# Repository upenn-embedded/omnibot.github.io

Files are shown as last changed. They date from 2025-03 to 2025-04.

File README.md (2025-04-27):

<div id="slideshow" style="width:100%; max-width:700px; margin: auto; position: relative; height: 450px;">
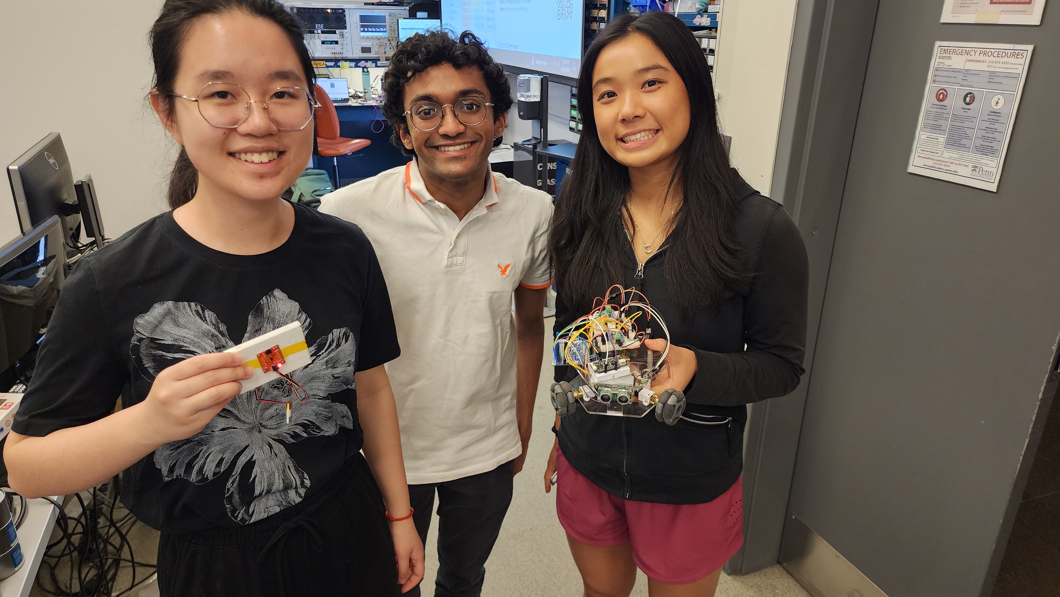
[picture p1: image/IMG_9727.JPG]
  
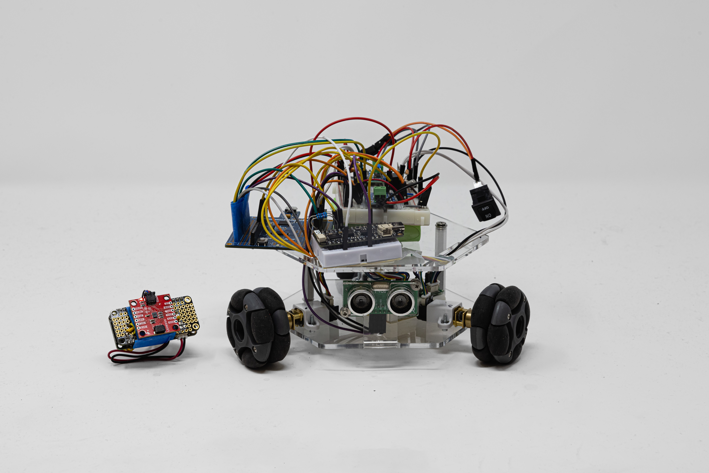
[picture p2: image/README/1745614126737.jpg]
  
  
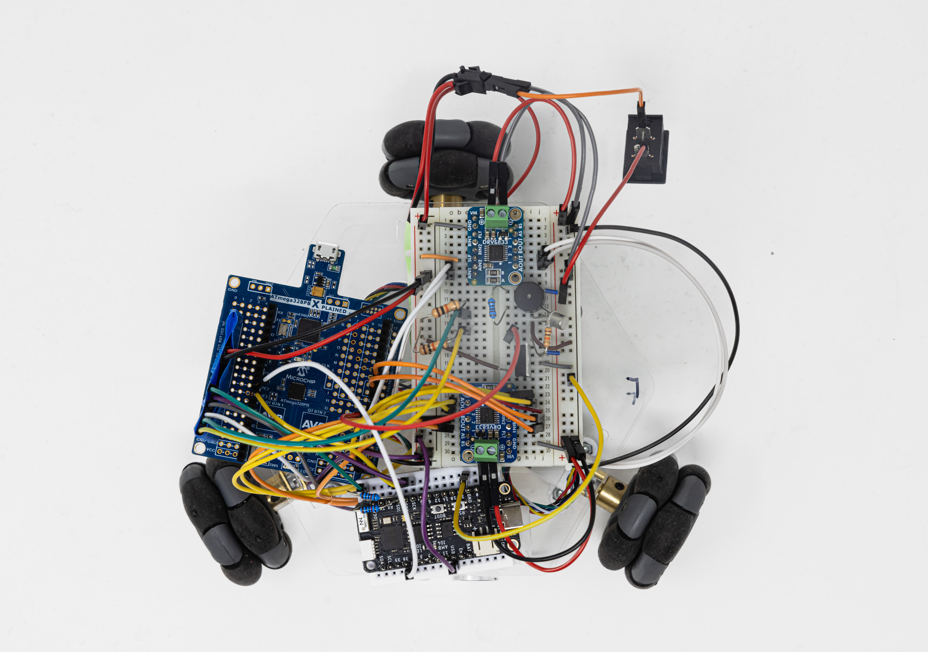
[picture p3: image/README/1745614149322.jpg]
  
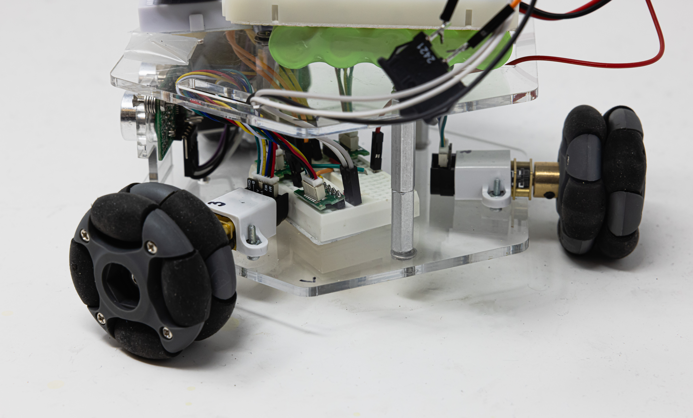
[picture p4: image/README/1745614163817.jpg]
  
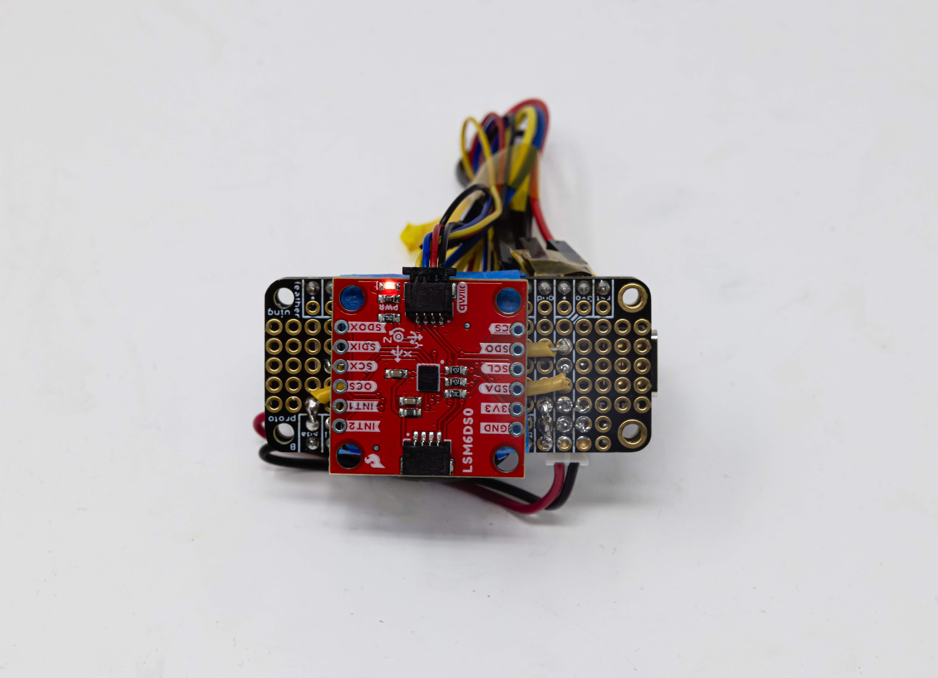
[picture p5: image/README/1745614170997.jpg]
  
  
</div>

<script>
let slides = document.querySelectorAll('#slideshow img');
let current = 0;
setInterval(() => {
  slides[current].style.opacity = 0;
  current = (current + 1) % slides.length;
  slides[current].style.opacity = 1;
}, 3000); // changes every 3 seconds
</script>

<br><br><br>

# final-project-OmniBot
    * Team Number: Team 9
    * Team Name: Oranges
    * Team Members: Izzy, Helena, and Vidhu
    * GitHub Repository URL: [https://github.com/upenn-embedded/final-project-s25-oranges](https://github.com/upenn-embedded/final-project-s25-oranges)
    * GitHub Pages Website URL: [https://upenn-embedded.github.io/omnibot.github.io/](https://upenn-embedded.github.io/omnibot.github.io/)

## Final Project Proposal

### 1. Abstract

Our final project is a gesture controlled omnidirectional robot designed to enable users to control a mobile robot’s movement using intuitive hand gestures. The robot will use omni wheels for enhanced maneuverability, allowing for movement in multiple directions (forward, backward, lateral, and diagonal) without the need for steering or reorientation. This is unlike traditional wheels, which require turning to change direction. Additionally, the OmniBot will include a collision detection system using an ultrasonic sensor that triggers a buzzer when obstacles are detected.

### 2. Motivation

Controlling robots using traditional joysticks or remotes can often be challenging and unintuitive, especially for new users. To address this, our project introduces a gesture-based control system that simplifies robot navigation while enhancing flexibility and precision through the use of omni wheels. The robot has the ability to move smoothly in multiple directions, including lateral and diagonal motion. Additionally, the inclusion of a collision detection system enhances the project's safety features by enabling the robot to identify and respond to nearby obstacles. These features make the project particularly valuable in practical applications like exploration and assistive robots for hazardous. The combination of intuitive gesture control and omni wheel movement offers a unique blend of precision, responsiveness, and user-friendly control.

### 3. System Block Diagram

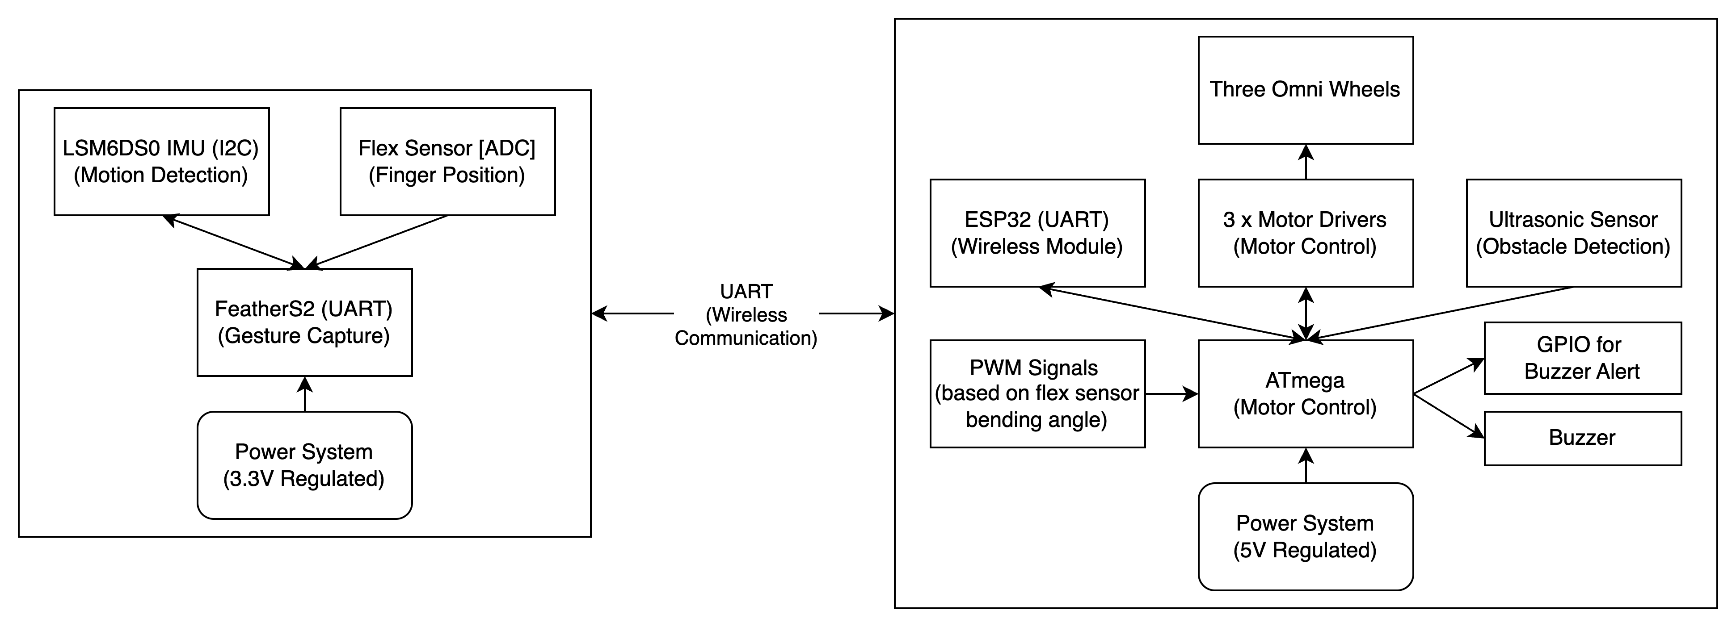
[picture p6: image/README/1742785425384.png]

Our system consists of two primary subsystems: the **Gesture Capture System** and the **Motor Control System** for the OmniBot. They utilize various communication protocols including I2C, ADC, UART, PWM, and GPIO. Additionally, regulated power supplies are integrated into both subsystems to deliver stable voltage levels.

The **Gesture Capture System** is centered around FeatherV2/FeatherS2, which manages both sensor inputs and wireless data transmission. It will handle gesture capture by interfacing with the LSM6DS0 IMU and Flex Sensor, while simultaneously transmitting control data to the OmniBot's ESP32 module via UART.

LSM6DS0 IMU is responsible for detecting hand motion and orientation. It uses the I2C to communicate with FeatherV2. The Flex Sensor detects the degree of bending in the user's fingers, then it generates an analog voltage that is read directly by the FeatherV2’s ADC. The ADC values are mapped to speed control commands, allowing different modes of motor speed with intuitive control. A FeatherS2 will be used to receive the data from the FeatherV2 via ESP-NOW and transmit the IMU values to the ATMega via SPI.

The **Motor Control System** is built around the ATmega328PB microcontroller, which handles motor control, obstacle detection, and alert systems. The FeatherS2 is mounted on the OmniBot and is the wireless receiver, communicating with the FeatherV2 on the wearable controller.

Motor control is achieved using two motor drivers (each driver can control 2 motors) that interface with ATMega. The motor drivers then manage the three omni wheels respectively, enabling movement in multiple directions. The ATMega generates PWM signals that control the direction of the motors and the speed is controlled through the duty cycle. The duty cycle will dynamically adjust based on the bending angle from the flex sensor and motor direction will change depending on the hand motion detected from the IMU.

The rover also features an ultrasonic sensor for obstacle detection. The sensor communicates with ATMega using GPIO pins for both the trigger and echo signals. When an obstacle is detected within a specified range, the ATMega will activate a buzzer via a dedicated GPIO output, alerting the user of the presence of an obstacle.

For the communication protocol, I2C links LSM6DS0 IMU to FeatherV2. The ADC on FeatherV2 is used to read variable voltage signals from the Flex Sensor. ESP-NOW is employed for wireless communication between the two Feather boards. ATMega generates PWM signals at different duty cycles to modulate motor speed and direction. GPIO connections are used for the ultrasonic sensor and the buzzer.

For power regulation, the Feather requires a 3.3V regulated power supply. Meanwhile, the 5V regulated power supply in the rover system delivers stable power to the ATMega328PB, motor drivers, ultrasonic sensor, and buzzer. A 6V battery is used to power our entire system. The motors we use are 6V and are able to pull as much current as needed from the battery pack. A 5V voltage regulator is used to buck down the 6V to 5V for our ATMega and peripherals. This separation of power systems ensures reliable performance, minimizes electrical noise, and protects components from voltage instability.

### 4. Design Sketches

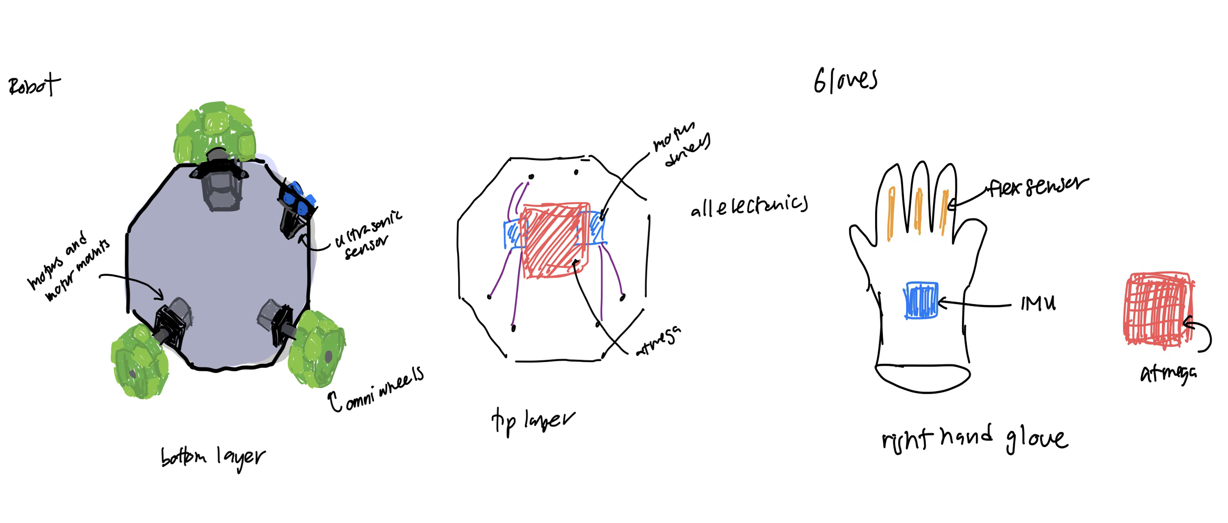
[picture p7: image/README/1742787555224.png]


For our design, the OmniBot's base uses omni wheels for enhanced motion in multiple directions. The use of an ultrasonic sensor for obstacle detection ensures improved environmental awareness. The top layer of the robot houses all essential electronics, including the ATMega board, motor drivers, and power distribution system. On the glove controller, the IMU is positioned centrally on the back of the hand to accurately detect wrist movements, and the flex sensors are embedded along the fingers to track bending angles for speed control.

### 5. Software Requirements Specification (SRS)

The software for the gesture-controlled rover robot will be able to process real-time motion and detect different gestures, wirelessly transmit commands, and be able to precisely control the rover. This can be broken down into three different subsystems:  gesture controller, rover control system, and collision detection system. The wearable gesture controller detects user gestures and transmits these movements wirelessly. The rover control system will be able to intercept these commands and control the rover's movement using predefined gesture mappings. The collision detection system monitors the rover/s surroundings and alerts the users of any obstacles. Key requirements include gesture recognition accuracy, reliable wireless communication, precise motor control, and responsive collision detection

**5.1 Definitions, Abbreviations**

*IMU (Inertial Measurement Unit):* A sensor that combines an accelerometer and a gyroscope to track orientation, acceleration, and angular velocity. In this project, it is used to detect hand gestures such as tilts and wrist rolls.

*Flex sensor:* A sensor that changes its resistance based on the amount of bending or flexing. It is used here to detect finger position and aid in gesture control.

*Feather ESP32:* The wireless communication module using ESP-NOW to transmit data between the wearable controller and the robot.

*Ultrasonic Sensor:* A distance sensor that uses sound waves to detect objects. It is used here for obstacle detection on the robot.

**5.2 Functionality**

<table>
  <thead>
    <tr>
      <th style="width:100px;">ID</th>
      <th>Description</th>
    </tr>
  </thead>
  <tbody>
    <tr>
      <td>SRS-01</td>
      <td>The IMU and flex sensors shall track predefined hand gestures (forward, backward, left, and right tilt, wrist roll, and open palm) within 200ms.</td>
    </tr>
    <tr>
      <td>SRS-02</td>
      <td>The ATmega328PB shall process the IMU data and classify gestures based off of certain threshold values correctly.</td>
    </tr>
    <tr>
      <td>SRS-03</td>
      <td>The ESP32 will transmit gesture data from the user to the robot with latency &lt; 200ms.</td>
    </tr>
    <tr>
      <td>SRS-04</td>
      <td>The robot shall have three speed modes controlled based on the angular velocity detected from wrist rolling.</td>
    </tr>
    <tr>
      <td>SRS-05</td>
      <td>The ultrasonic sensor shall detect obstacles within 5–100 cm. If an obstacle is within 20 cm, the robot will stop, ignore commands, and the LED will turn red. Once cleared, the robot resumes movement, and the LED turns green.</td>
    </tr>
    <tr>
      <td>SRS-06</td>
      <td>The entire system will run independently on the ATmega328PB without the need of an external computer.</td>
    </tr>
    <tr>
      <td>SRS-07</td>
      <td>If wireless connection is lost, the robot shall automatically stop within 500ms.</td>
    </tr>
  </tbody>
</table>

### 6. Hardware Requirements Specification (HRS)

The hardware for the gesture controller rover will allow it to move freely in many directions as well as sense the motion of the controller. Additionally, it will be able to sense obstacles ahead using an ultrasonic sensor.

**6.1 Definitions, Abbreviations**
*Feather ESP32:* Board for wireless communication

*ATMega328PB:* Main microcontroller on the rover

**6.2 Functionality**

| ID | Description |
| --- | --- |
| HRS-01 | The rover must be able to run for at least 15 minutes continuously. |
| HRS-02 | The ultrasonic sensor must be able to accurately detect obstacles within 5-100 cm. |
| HRS-03 | The motors must be able to move the rover at varying speeds. |
| HRS-04 | The rover must be able to move in perpendicular directions without needing to turn using the omni wheels. |
| HRS-05 | The flex sensor must be able to control the speed of the rover using an ADC. |
| HRS-06 | Motion of the IMU must translate into motion of the rover. |
| HRS-07 | The two ESP32 boards must be able to wirelessly communicate with each other directly. |
| HRS-08 | The ESP32 and ATMega328PB must be able to communicate using SPI. |

### 7. Bill of Materials (BOM)
This is a general list of our bill of materials. A more detailed list can be found [here](https://docs.google.com/spreadsheets/d/1VVz9bghLVpC_rwVTz9ZApd166kRQwFx1JgdSo3LERfQ/edit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). We used an ATMega329PB, Feather ESP32 V2, Feather ESP32 S2, LM6DS0 IMU, US-10 Ultrasonic sensor, 3 6V Polulu motors with motor mounts and enocder wires, 6V battyer, 2 DRV8871 motor drivers, and 3 omni wheels.

### 8. Final Demo Goals

On Demo Day, we will build an obstacle course for our rover to test in. Someone will wear the controller and manuver the rover around obstacles. Part of the test will include getting close to an obstacle and stopping before a collision. The test will conclude when the rover is successfully able to get to the end of the obstacle course.

### 9. Sprint Planning

| Milestone  | Functionality Achieved |
| --- | --- | --- |
| Sprint #1  | 1. Developed Wearable Controller Prototype using the FeatherS2.<br />2. Implemented motion sensing algorithms with the  LSM6DS0 IMU.<br />3. Integrated the Flex Sensor for ADC-based speed control.<br />4. Developed basic motor control firmware for the ATmega using PWM signals for speed and direction. | 
| Sprint #2  | 1. Established UART Communication between the two FeatherS2 boards.<br />2. Integrated gesture detection logic with motor speed control via PWM signals.<br />3. Assembled hardware components: Motor Drivers, Omni Wheels, and Power Systems.<br />4. Conducted movement tests to verify functionality. |
| MVP Demo | 1. Developed and tested the Ultrasonic Sensor with the ATmega328PB.<br />2. Integrated obstacle detection logic to trigger the Buzzer via GPIO.<br />3. Refined gesture detection algorithms to improve accuracy.<br />4. Fine-tuned Flex Sensor ADC values for smoother speed control. | 
| Final Demo | 1. Conducted full system integration for all subsystems.<br />2. Performed system calibration for accurate motion control, speed adjustment, and obstacle detection.<br />3. Conducted extensive performance testing for stability. |

### Prototyping Images
<!-- row 1 -->
<div style="display: flex; justify-content: center; gap: 20px;">
  <div style="text-align: center;">
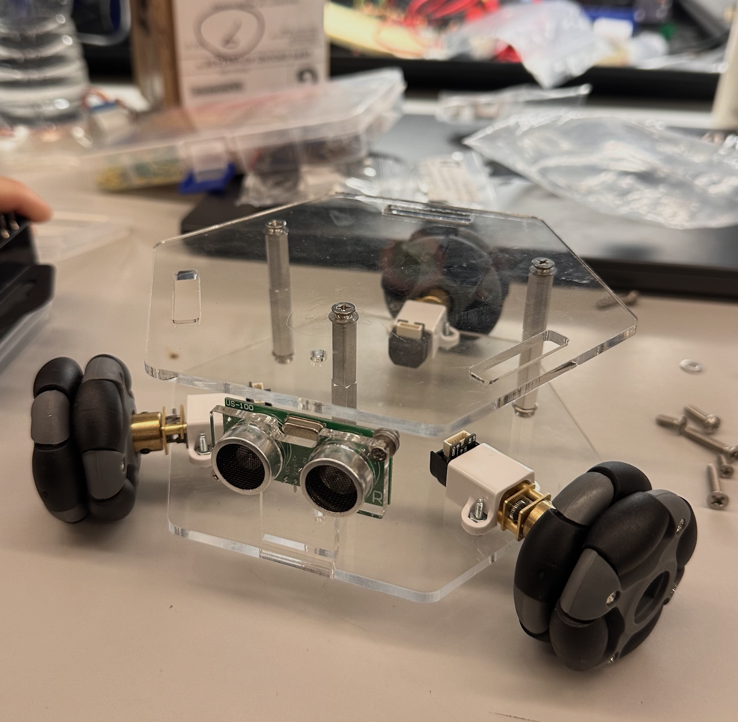
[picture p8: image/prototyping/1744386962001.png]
    <br>
    <sub>Robot Chassis</sub>
  </div>

  <div style="text-align: center;">
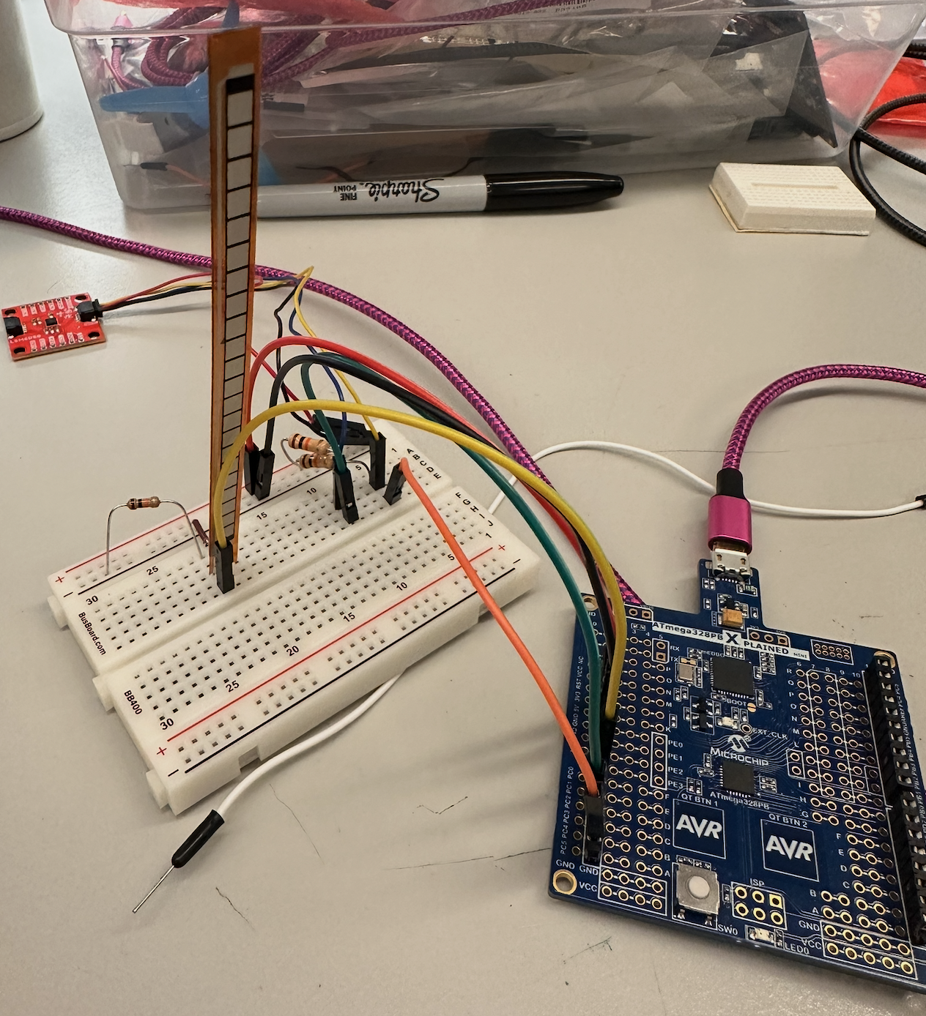
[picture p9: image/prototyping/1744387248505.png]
    <br>
    <sub>Flex Sensor Wiring</sub>
  </div>

  <div style="text-align: center;">
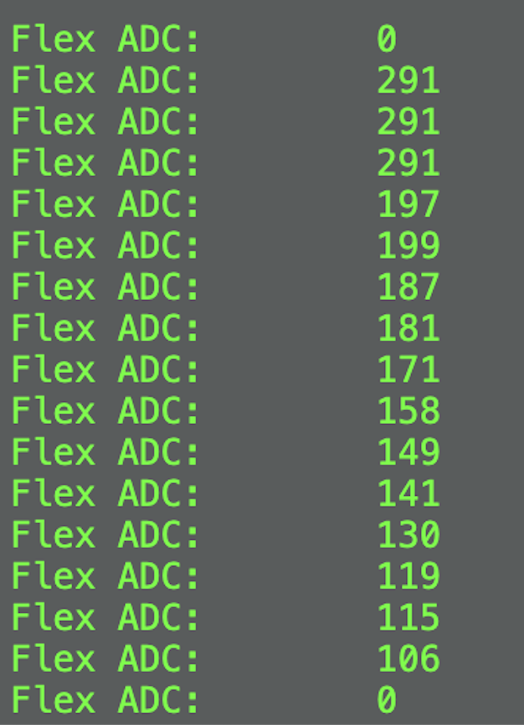
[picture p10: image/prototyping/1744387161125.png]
    <br>
    <sub>Flex Sensor ADC</sub>
  </div>

  <div style="text-align: center;">
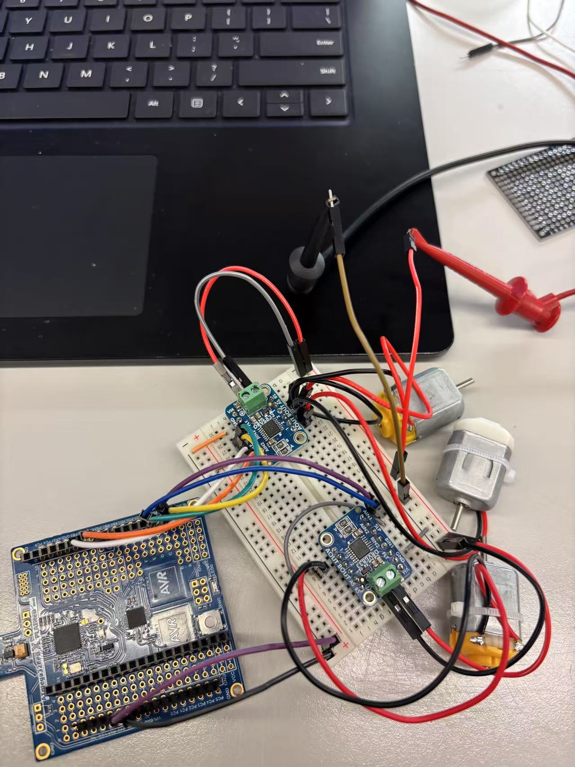
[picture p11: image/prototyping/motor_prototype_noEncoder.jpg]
    <br>
    <sub>Motor Driver Setup</sub>
  </div>
</div>

<br>

<!-- row 2 -->
<div style="display: flex; justify-content: center; gap: 20px;">
  <div style="text-align: center;">
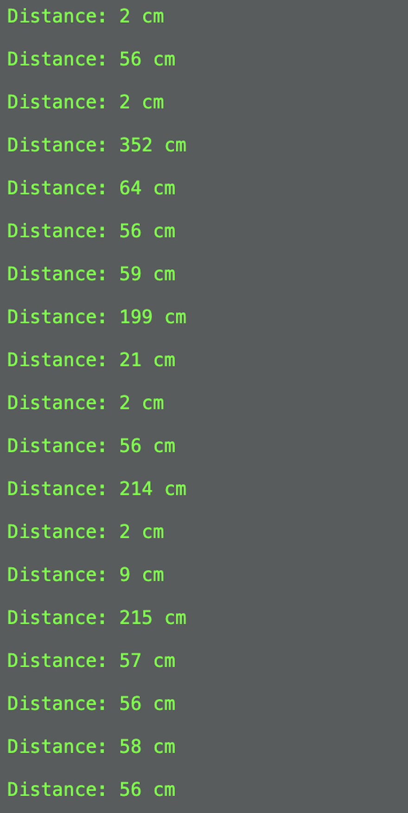
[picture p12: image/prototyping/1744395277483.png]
    <br>
    <sub>Distance Measurements</sub>
  </div>

  <div style="text-align: center;">
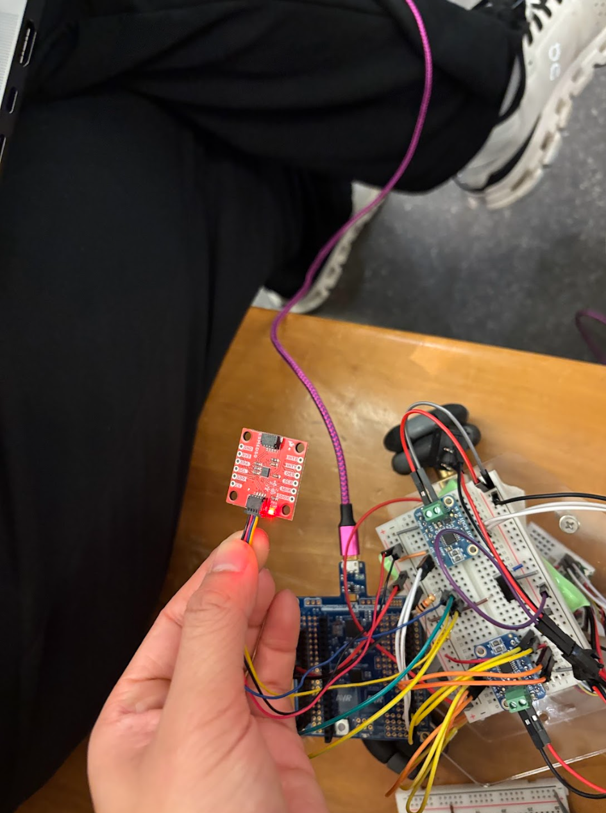
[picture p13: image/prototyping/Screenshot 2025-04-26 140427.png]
    <br>
    <sub>IMU Calibration</sub>
  </div>

  <div style="text-align: center;">
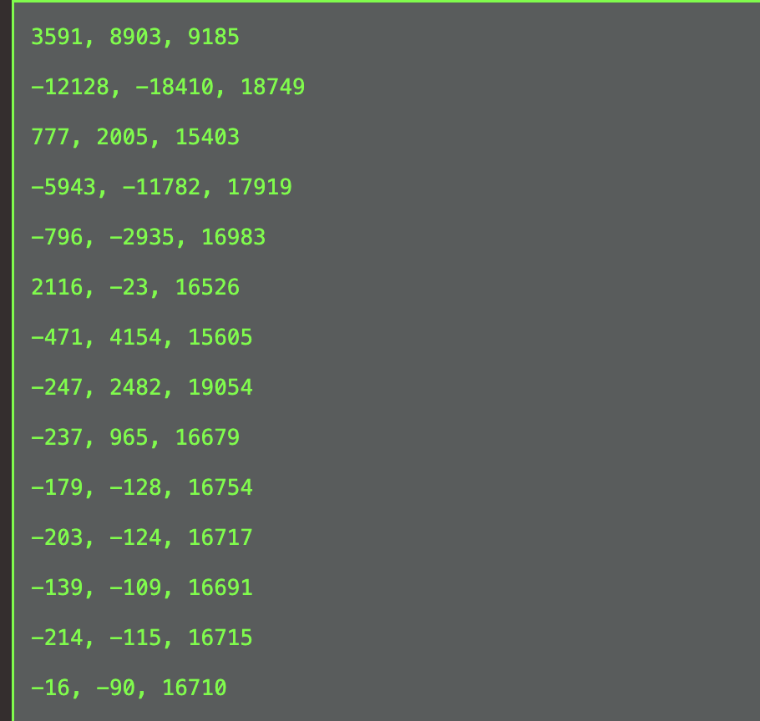
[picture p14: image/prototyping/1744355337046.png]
    <br>
    <sub>IMU Calibration Output</sub>
  </div>

  <div style="text-align: center;">
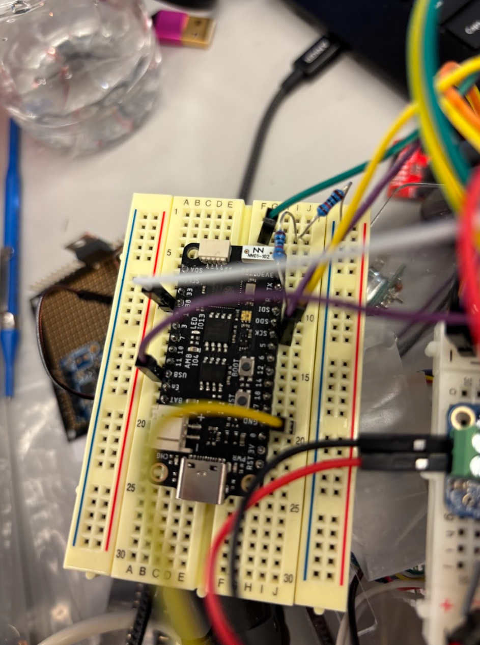
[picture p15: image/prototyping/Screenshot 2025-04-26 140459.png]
    <br>
    <sub>Feather S2 on OmniBot</sub>
  </div>
</div>

<br>

<!-- row 3 -->
<div style="display: flex; justify-content: center; gap: 20px;">
  <div style="text-align: center;">
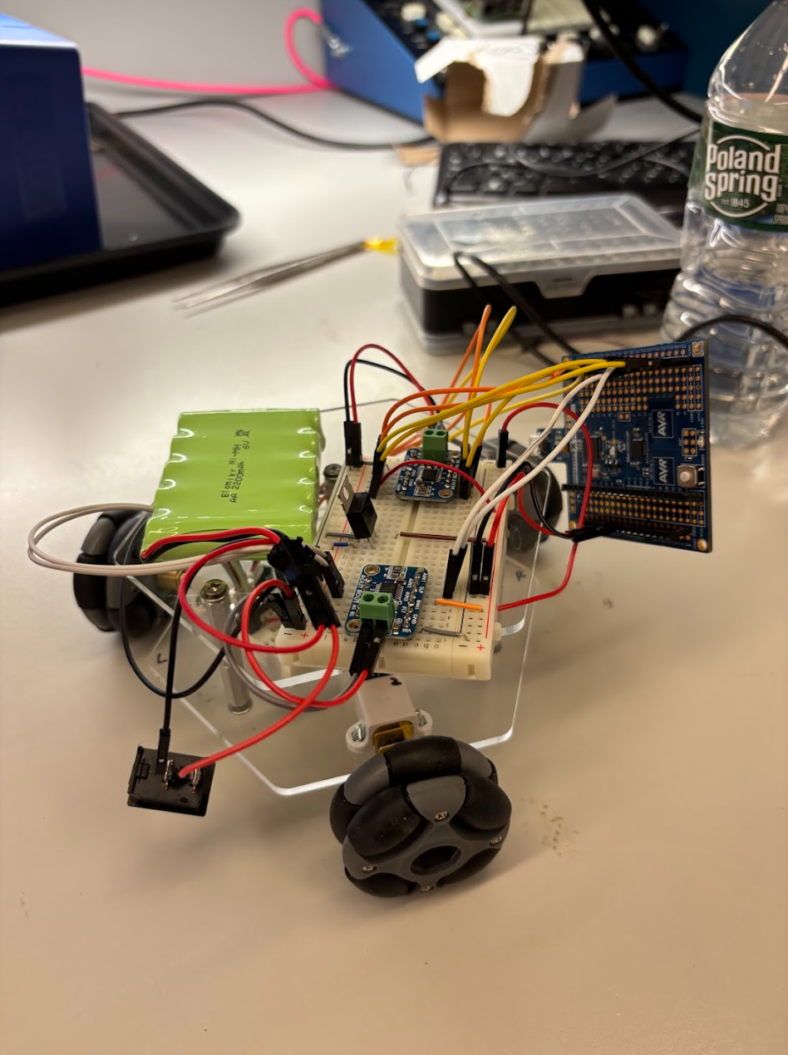
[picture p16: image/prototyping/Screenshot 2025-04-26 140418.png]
    <br>
    <sub>Motor Assembly</sub>
  </div>

  <div style="text-align: center;">
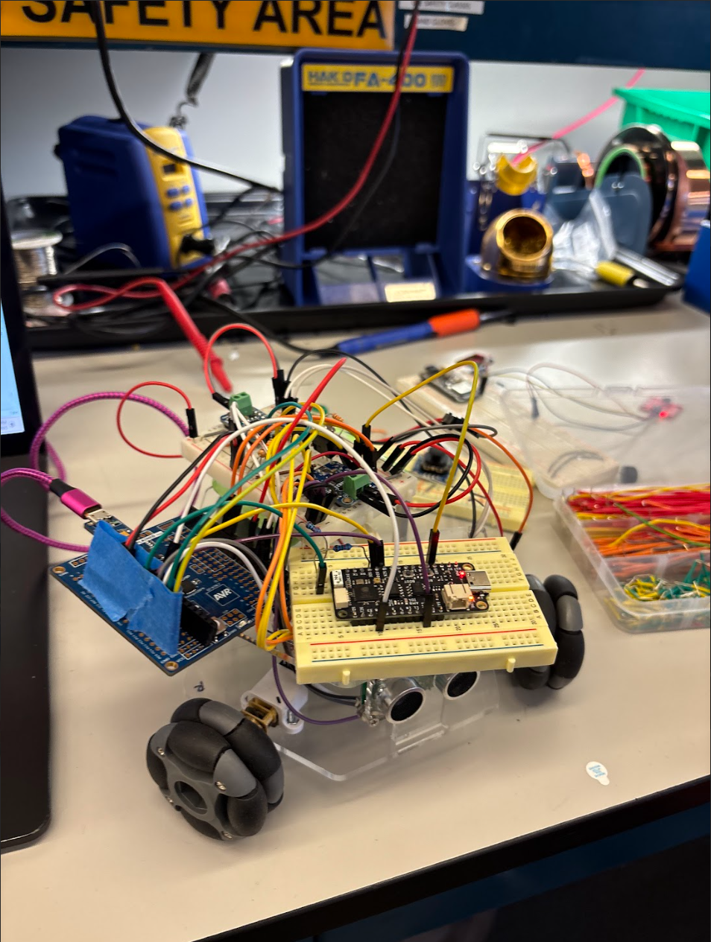
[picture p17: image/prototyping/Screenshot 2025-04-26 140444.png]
    <br>
    <sub>Integration</sub>
  </div>

  <div style="text-align: center;">
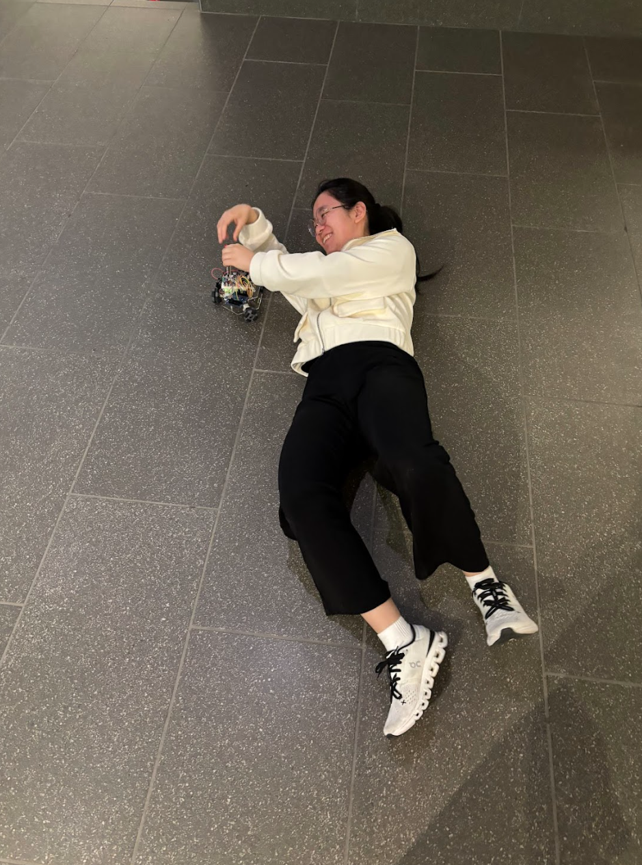
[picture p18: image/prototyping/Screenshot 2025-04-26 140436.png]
    <br>
    <sub>Testing!!</sub>
  </div>

  <div style="text-align: center;">
    <br>
    <sub>MVP Assembly</sub>
  </div>
</div>

<br>

### Wiring Diagrams

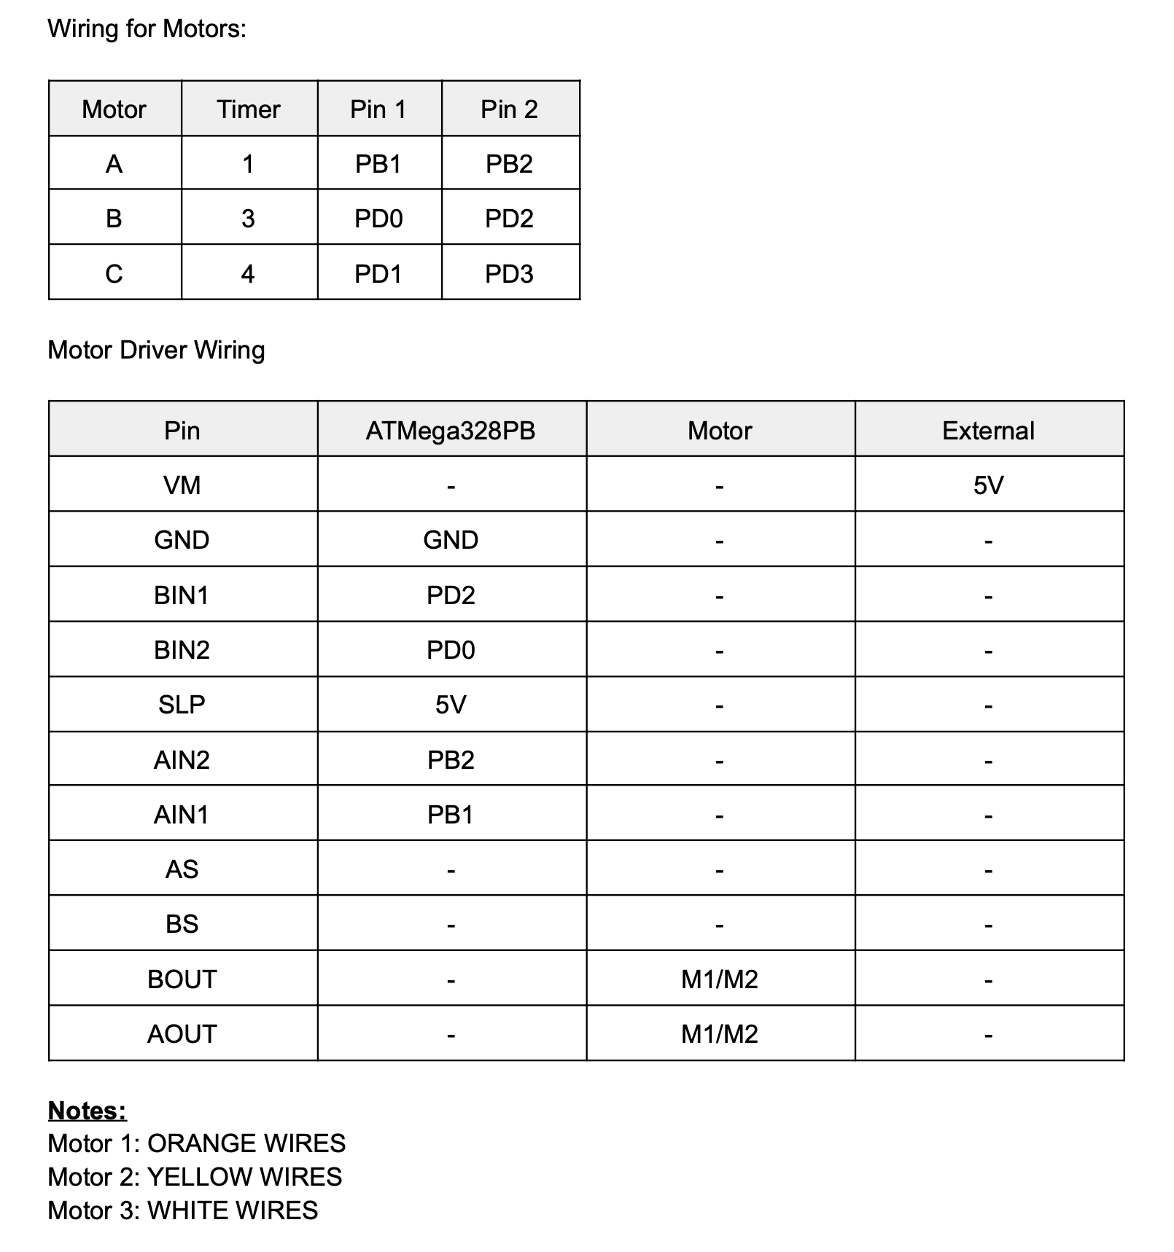
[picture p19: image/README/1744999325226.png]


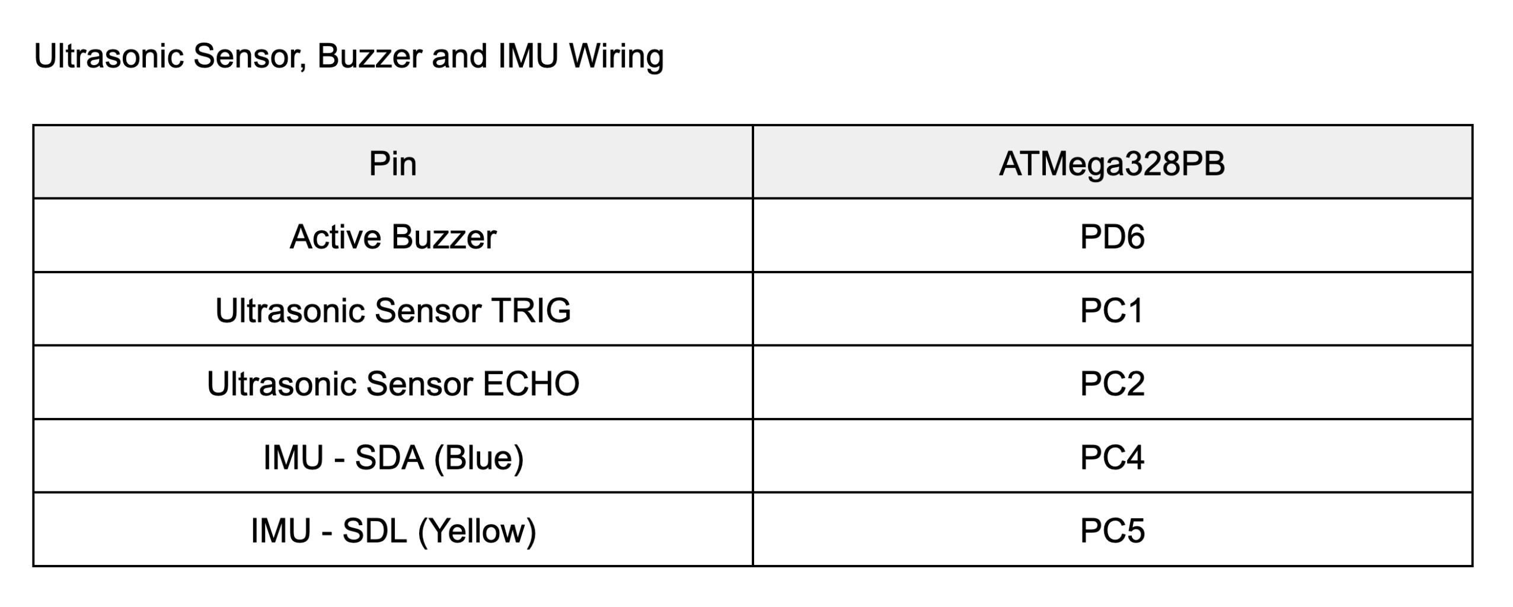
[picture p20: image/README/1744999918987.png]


IMU Calibration Data

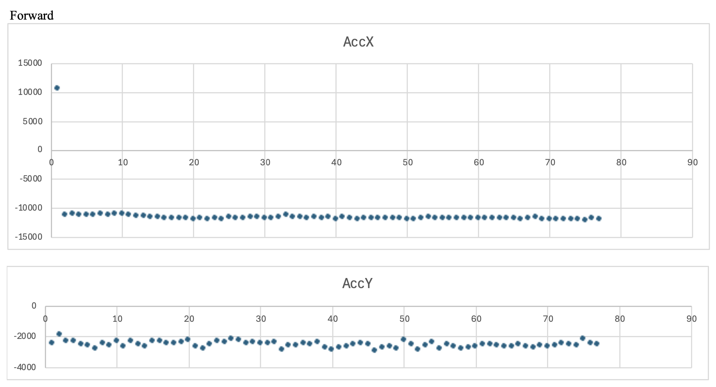
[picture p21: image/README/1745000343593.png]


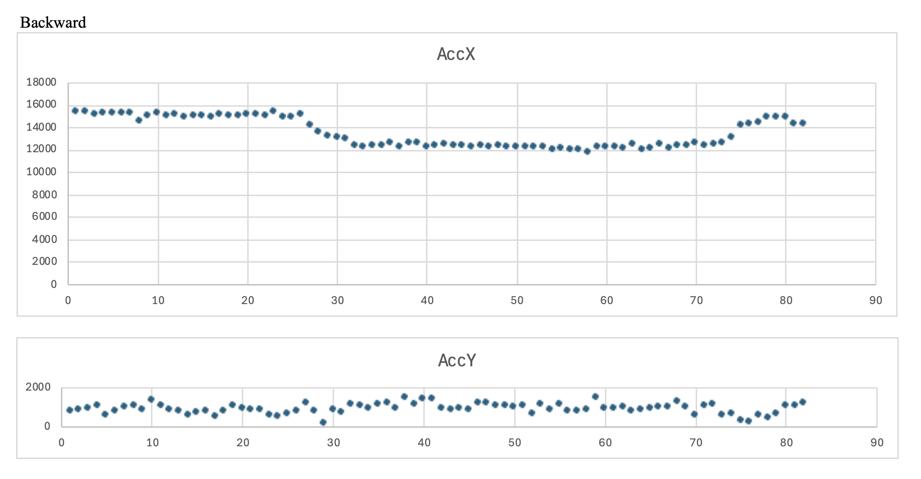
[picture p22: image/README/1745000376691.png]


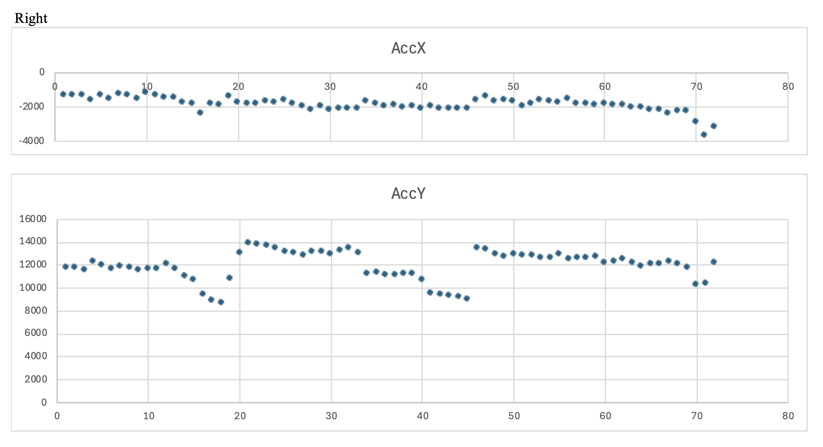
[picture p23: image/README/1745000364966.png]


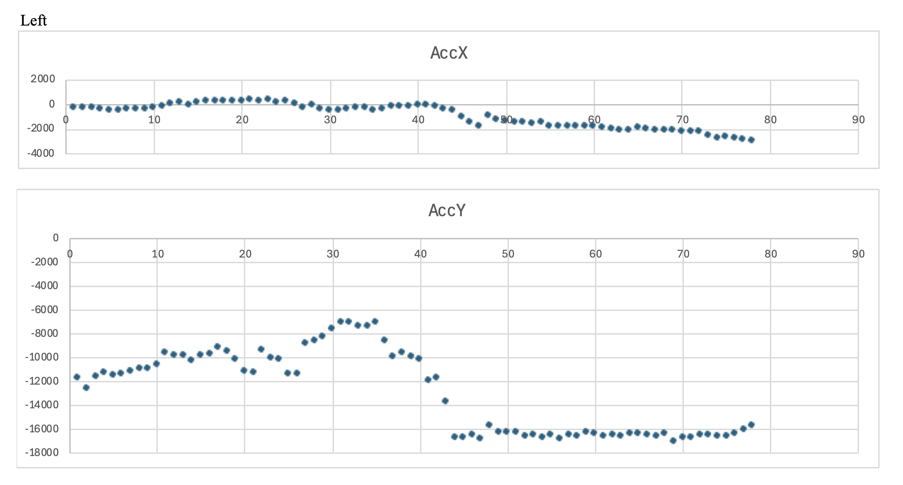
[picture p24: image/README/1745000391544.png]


Based on the above data collected, our calibrated control for IMU is:

if (x < -7500 && y > -4000 && y < 4000) → "move forward"  
if (x > 7500 && y > -4000 && y < 4000) → "move backward"  
if (x > -4000 && x < 4000 && y > 7500) → "move right"  
if (x > -4000 && x < 4000 && y < -7500) → "move left"  

### **Final OmniBot**

<div align="center">
  <iframe width="700" height="400" src="https://www.youtube.com/embed/BRfWkiYQ0kc" frameborder="0" allow="accelerometer; autoplay; clipboard-write; encrypted-media; gyroscope; picture-in-picture" allowfullscreen></iframe>
</div>

We were successfully able to complete our entire project and have a reliable working demo. Our final OmniBot was able to move in all four basic directions based on the tilt of the controller. It could also stop if an obstacle was detected in front of it. When this obstacle is detected, the buzzer will sound to alert the user, and the user can only move the OmniBot backward, left, and right. Many of our classmates and friends played around with the OmniBot and found it very fun!

**Technical Details**
**Robot Movement**: 3 timers were configured to drive the motors. Timer 1 is used for Motor 1, Timer 3 is used for Motor 2, and Timer 4 is used for Motor 3. These three timers are all 16-bit timers which make the configuration of each motor identical. For timer 1, we use two OCRA/B values to send different PWM signals to control the direction and speed. For timer 3 and 4, we found that the second OCRB pin overlapped with each other (both used PD2 on the ATMega), thus we use one PWM pin to output variable duty cycles and a GPIO direction pin sets motor direction (HIGH/LOW). We wrote custom functions such as `move_forward()`, `move_backward()`,` move_left()`, and `move_right()` for each direction of the robot. Each function will send different duty cycles to each wheel to control it in the four basic directions. To control the speed, the ratio of duty cycle for each wheel can be scaled up or down. Since the robot is three-wheeled, we accounted for the drift of the robot through a `drift_correction()` function or else the robot will make a lot of circles instead of going in the desired direction! If the left or right direction is detected,  `drift_correction()` will be called which alternates the PWM outputs of one motor slightly back and forth to "steer" the OmniBot towards a straighter left or right direction. This happens periodically. We implemented directional states, so the OmniBot can keep track of which direction it is currently going in and only changes motor movements if a new state is detected from the user IMU controller.

**IMU Calibration**: To implement the IMU so that the OmniBot can move based off of the IMU tilting degree, we collected data for the x and y acceleration values on the IMU at different tilting degrees. We plotted these values, shown in earlier figures, to determine different classification values. We were able to observe clear differences of the x and y acceleration when the IMU was stationary or tilted. We also observed that as the degree of tiling increases, the absolute value of the IMU output also increases. With these values, we were able to implement conditional clauses that call the right direction functions to activate the correct PWM signals and duty cycles for the respective motors.

**Controller**
The controller is composed of the IMU, which is communicating the accelerometer data to the Feather ESP32 V2 via I2C. This data was calibrated through processing several datasets of both the x and y accelerometer data depending on the tilting of the IMU, as discussed above. Once the IMU is calibrated, then the robot can correctly identify the tilt of the controller and act accordingly. Through creative soldering, we were able to make the controller as small as the Feather ESP32 S2 which is roughly 2.5 in x 1 in (super small!).

**Communication**
The IMU is collecting the accelerometer data from the controller. This data is sent processed in the Feather ESP32 V2 and sent to the Feather ESP32 S2 on the robot, wirelessly, through the ESP-NOW protocol. The Feather on the robot then communicates the data it received to the ATMega328PB through SPI, so the robot can act accordingly.

**Ultrasonic Sensor**
There is an ultrasonic sensor mounted on the front of our robot. When it detects a distance less than 20cm, it will sound a buzzer and will not let you move forward even if the controller is in the forward position. The robot will only be able to move back, left, and right until it is clear of the blocking object. The buzzer we are using is an active buzzer which beeps if the pin is in the HIGH state. We use polling and not interrupts so that the ATMega continuously checks the ECHO pin to see if the distance is below threshold value.

### Software Requirments Results
<table>
  <thead>
    <tr>
      <th style="width:100px;">ID</th>
      <th>Description</th>
      <th>Validation Outcome</th>
    </tr>
  </thead>
  <tbody>
    <tr>
      <td>SRS-01</td>
      <td>The IMU 3-axis acceleration will be measured with 16-bit depth every 100 milliseconds +/-10 milliseconds.</td>
      <td>Confirmed, logged output from the MCU is saved to "validation" folder in GitHub repository.</td>
    </tr>
    <tr>
      <td>SRS-02</td>
      <td>The ATmega328PB shall process the IMU data and classify gestures based off of certain threshold values correctly.</td>
      <td>Confirmed, we tested and calibrated the threshold values based on the values outputted by the IMU.</td>
    </tr>
    <tr>
      <td>SRS-03</td>
      <td>The ESP32 will transmit gesture data from the user to the robot with latency &lt; 200ms.</td>
      <td>Confirmed, the robot is able to respond within 200ms, meaning communication latency is within requirement.</td>
    </tr>
    <tr>
      <td>SRS-04</td>
      <td>The robot shall have three speed modes controlled based on the angular velocity detected from wrist rolling.</td>
      <td>Not met, the robot speed is constant in each direction. Speed modes were not implemented due to time constraints.</td>
    </tr>
    <tr>
      <td>SRS-05</td>
      <td>The ultrasonic sensor shall detect obstacles within 5–100 cm. If an obstacle is within 20 cm, the robot will stop, ignore commands, and the LED will turn red. Once cleared, the robot resumes movement, and the LED turns green.</td>
      <td>Confirmed, the ultrasonic sensor stops the robot when within 20 cm. We implemented a buzzer instead of an LED for clearer feedback to the user.</td>
    </tr>
    <tr>
      <td>SRS-06</td>
      <td>The entire system will run independently on the ATmega328PB without the need of an external computer.</td>
      <td>Confirmed, the robot is fully autonomous and operates only using the ATMega328PB (see demo video).</td>
    </tr>
    <tr>
      <td>SRS-07</td>
      <td>If the wireless connection is lost, the robot shall automatically stop within 500 ms.</td>
      <td>Not met due to time constraints. Planned for future iterations.</td>
    </tr>
  </tbody>
</table>

### Hardware Requirements Results

<table>
  <thead>
    <tr>
      <th style="width:100px;">ID</th>
      <th>Description</th>
      <th>Validation Outcome</th>
    </tr>
  </thead>
  <tbody>
    <tr>
      <td>HRS-01</td>
      <td>The rover must be able to run for at least 15 minutes continuously.</td>
      <td>Confirmed. We turned the robot ON continuously for 15 minutes and verified that the battery could sustain operation.</td>
    </tr>
    <tr>
      <td>HRS-02</td>
      <td>A distance sensor shall be used for obstacle detection. The sensor shall detect obstacles at a maximum distance of at least 10 cm.</td>
      <td>Confirmed. The ultrasonic sensor was able to detect obstacles up to 15 cm. See serial output and demo video.</td>
    </tr>
    <tr>
      <td>HRS-03</td>
      <td>The motors must be able to move the rover at varying speeds.</td>
      <td>Not met. The rover moves at a constant speed in all directions, although individual motors run at slightly different speeds. See reflection section #5 for more details.</td>
    </tr>
    <tr>
      <td>HRS-04</td>
      <td>The rover must be able to move in perpendicular directions without needing to turn using the omni wheels.</td>
      <td>Confirmed. The robot can move left and right without rotating, as demonstrated in the video.</td>
    </tr>
    <tr>
      <td>HRS-05</td>
      <td>The flex sensor must be able to control the speed of the rover using an ADC.</td>
      <td>Not met. We decided not to implement the flex sensor since speed control was not fully implemented.</td>
    </tr>
    <tr>
      <td>HRS-06</td>
      <td>Motion of the IMU must translate into motion of the rover.</td>
      <td>Confirmed. IMU tilting directly controls the robot's movement. (See demo video)</td>
    </tr>
    <tr>
      <td>HRS-07</td>
      <td>The two ESP32 boards must be able to wirelessly communicate with each other directly.</td>
      <td>Confirmed. The ESP32 boards successfully transmit and receive data wirelessly. Validated through Arduino serial monitor and testing screenshots.</td>
    </tr>
    <tr>
      <td>HRS-08</td>
      <td>The ESP32 and ATmega328PB must be able to communicate using SPI.</td>
      <td>Confirmed. The Feather sends IMU data to the ATmega328PB through SPI. Validated through UART debug output and video demonstration.</td>
    </tr>
  </tbody>
</table>

### Final Images

<div align="center">

Overall Look  
<br>



</div>

<br>

<div align="center">

Front View  
<br>



</div>

<br>

<div align="center">

Back View  
<br>



</div>

<br>

<div align="center">

Top View  
<br>


</div>

<br>

<div align="center">

Bottom Layer Details (Motors)  
<br>



</div>

<br>

<div align="center">

IMU Detail  
<br>

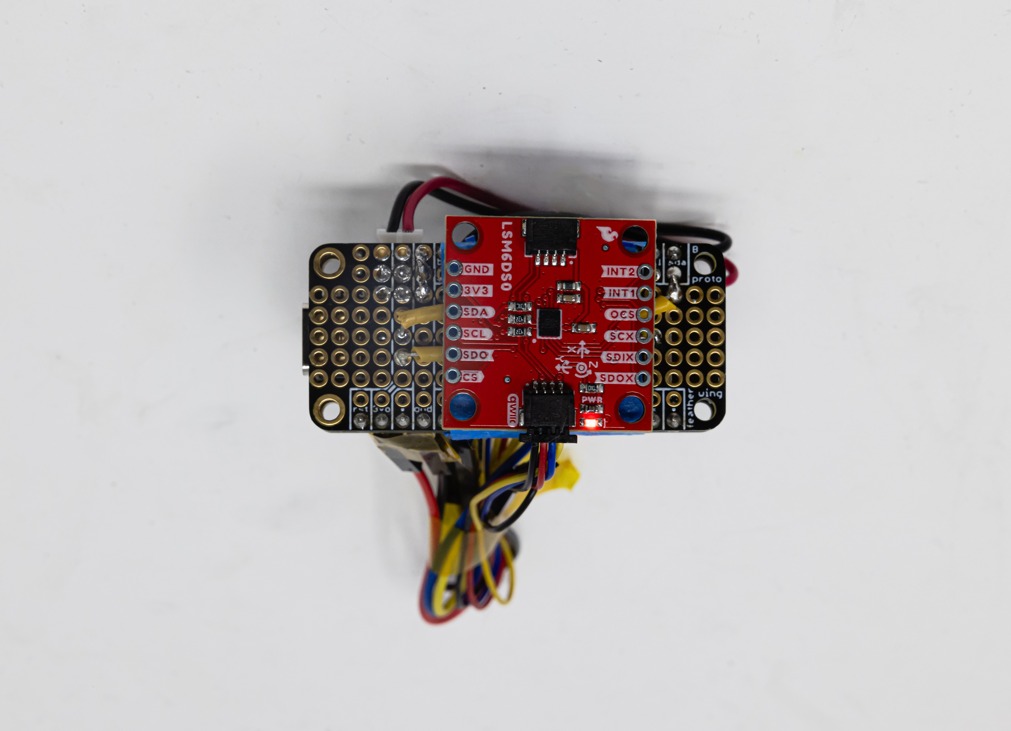
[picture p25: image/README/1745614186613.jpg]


</div>

### References
In our MPLAB code, we used the standard C libraries including `stdio.h`, for input output, `avr/io.h` and "`avr/interrupt.h`", for standard avr and interrupts, and `util/delay.h`, for delays.

In our Arduino code for our IMU and Feather communication via I2C and Feather to Feather communication through ESP-NOW, we used the libraries `Wire.h`, `esp_now.h`, and `WiFi.h`. `Wire.h` enables the I2C communication between the IMU and the Feather. It interfaces with the SDA and SCL lines of the IMU. We use `esp_now.h` to implement the ESP-NOW protocol which allows us to communicate from one Feather to another by sending and receiving data packets. The `WiFi.h` library is used to manage the Wifi connections that are needed for the ESP-NOW communication in the `esp_now.h` library.

### Conclusion

#### 1. What did you learn from it?

One of the key takeaways from this project was the importance of thoroughly mapping out all the internal components of the ATmega328PB  before starting integration. The chip has a limited number of shared resources, such as timers, and in our final design, we ended up using four of the five timers for various functions, including motor control, SPI communication, and the buzzer for the ultrasonic sensor. Because some timers are 8-bit while others are 16-bit, and each has different capabilities, it’s crucial to plan and communicate clearly which timers are assigned to which modules. We configured timers 1, 3, and 4 for the motors because they are all 16-bit timers which would make the motor configuration mostly the same for all three motors. Without proper planning, overlap usage would likely occur which would then require significant code changes, slowing down the integration process.

Another important takeaway was learning how unpredictable embedded systems development can be. Sometimes, components fail or behave unexpectedly, and pinpointing the root cause requires extensive testing and debugging. This includes probing signals with an oscilloscope and stepping through code carefully. For instance, when none of our motors were responding during SPI integration, we eventually discovered that the uart_init() function was unintentionally reconfiguring the timers used for motor control. Once, we commented out that line, everything worked!!

#### 2. What went well?

The IMU went well in controlling the direction of the robot's motion. It was able to distinguish each direction smoothly without confusion. The ultrasensor is also detecting object accurately without making annoying unwanted noises. Since we carefully assign the timers to motors and ultrasonic sensors and that the SPI communication did not require a timer, no integration conflict happened for the timers. Some pins had to be adjusted during integration, but eventually, we're able to utilize the correct PWM pins and GPIO pins correctly. The power manaagement for the robot (6V) battery was really successfully, since we didn't need to recharge it for the entirely of our project, which proves its durability.

Aside from that, the initial mechanical part in designing the robot's structure is also pretty successful since it's very steady when we're testing the robot, and the support for the ultrasonic sensor press-fit well wihout ever falling.

#### 3. What accomplishments are you proud of?

Our motors are able to transition very smoothly and react fairly between changes in directions. A big part of this was implementing *direction states* in the code. Initially, the motors would "think" every second and decide what direction they would move in. However, after implementing states, if the direction is the same, then the motors will continue to move in the same direction without stopping. This resulted in better transitions between different direction states as well as more control of the robot. Additionally, the given that it is a 3-wheel omnidrive robot, it is able to move left and right well. We implemented a drift_correction function that corrects for drift if it detects that the robot is moving left or right. This lets the robot move successfully to the left or right without making a circle.

#### 4. What did you learn/gain from this experience?

From this experience, we learned how to integrate multiple hardware subsystems into an integrated embedded system. It also helped us learn how each individual parts might interact in unexpected ways when combined. We gained how import UART debugging is. the feather SPI communication has been quite a big issue for us, since the high and low bits tend to mess around with each other, which output us completely random results on the serial monitor. Then, we print our the feather V2, S2 output and the signal that atmega's receiving separatingly on both arduino and MPLab. We also printed low and high bits separately and figured out the issue. We also learned how to structure data packets between two ESP32 Feather S2 boards.

We also learn more about the control and kinematics of three-wheel motion control. The robot is symmetric moving forward/backward, hence motion control is quite straightforward. However, for left and right motion, we implemented a drift motion of the third wheel that compensates for the error in motion. We also read some literature about kinematics of three wheel motion and its vector applications with encoders, but the algorithm is too complicated under the timeline, hence we'll plan to implement that for future explorations.

We also learned that integration was a very important step. Although all stages worked well separately, putting them all together usually produces unexpected behaviors. For instance, UART would crash the entire motor motion setup program, so that we have to test print statements and motions separately. But overall, we learn how to manage PWM signals, especially when dealing with multiple timer; the I2C and SPI communication between IMU, feather, and ATmega; using ADC pins and GPIO pins; using UART for debugging and verfication for separate stages etc.

##### 5. Did you have to change your approach?

We initially intended this robot to be controlled with the movements of your hand using a glove-mounted IMU. However, since we didn't order the glove hardware, we redesigned it to use a small Feather-sized controller instead. This means we couldn't implement the flex sensors that were originally planned to control the robot's speed.

The speed control would have required dynamically adjusting the ratio between the left and right motor duty cycles. This presents a problem because our drift correction function relies on very specific motor pulses. The correction works by applying brief, low-power motor pulses (just 48-55 duty cycle) that are barely strong enough to overcome static friction. If we tried to scale down the overall speed, these correction pulses would become too weak to overcome friction. At that point, the robot would lose its ability to drive straight and would instead start turning in circles because the drift correction would fail. Forward and backward pose no issue to speed control, but left and right have difficulty because of the drift correction. In further iterations, if we use encoder feedback to drive the left and rightward motion, then we will be able to adjust speed based off of the change in acceleration over time of the IMU.

#### 6. What could have been done differently?

We should have added more debugging checkpoints throughout the system before integration. This would have made it easier to test each component individually and quickly identify issues. Instead, we only added these debugging tools (like print statements on both Feathers and the ATMega328PB) after integration problems arose, which slowed our progress. Some key debugging features we implemented late included:

    * IMU data transfer verification
    * Direction classification checks
    * Ultrasonic sensor distance readings
    * LED indicators for motor activation

Additionally, we could have maintained a document listing frequent problems and their solutions. This would have saved time by preventing redundant debugging of issues we'd already solved.

#### 7. Did you encounter obstacles that you didn’t anticipate?

We didn't anticipate the communication between the robot and controller to take as long as it did. We accidentally used two different versions of the Feather. The Feather connected to the IMU is the ESP32 V2 version and the Feather on the robot is the ESP S2 version. We didn't realize that we were using two different versions, and the S2 code isn't able to run on the V2 version because it uses newer Arduino code that is not compatible with V2. After realizing that we are using two different versions and the Arduino code is not compatible, we were able to rewrite the FeatherV2 code so that it can communicate properly with the IMU via I2C. As for the Feather S2 communicating with the ATMega328PB through SPI so that the motors can react to the IMU position, we were sending over 2 8-bit packets of data to be processed by the ATMega. We found that sometimes, the x and y acceleration values printed in uart, after processed by the ATMega, followed the values we saw when calibrating the IMU. However, other times we found that the values were totally arbitrary which confused us a lot! We spent a of time debugging, and ended up realizing that when the Feathers reset, the high and low data packets may switch, so we have to process the values on the ATMega slightly differently depending on each case.

#### 8. What could be a next step for this project?

The next steps of the project can include integrating a smoother transition between different moving states of the robot. Currently, it is able to move forward, backward, left, and right and transition smoothly between these states. If we study the kinematics of a three wheel omnidrive robot more, we can implement smoother control of the robot. We can probably take the x and y vectors sent over by the IMU, and use a formula to calculate the direction of the controller, from this we can adjust the PWM and duty cycle of each motor so the robot moves in the desired direction. Additionally, the ultrasonic sensor requires a bit of thinking before it beeps and stop the robot. We could potentially integrate the sensor in a different way where it takes less time to think and can act quickly.

We can also work on reducing the bulkiness of the robot. The top of the robot has multiple breadboards to house the Feather, motor drivers, and ATMega328PB. We tried to use a protoboard to reduce the bulkiness; however, when we were testing this newly soldered, second set of components, it seemed that everything was shorting each other as the multimeter read 0V between VCC and GND. We are still unsure why this is happening, because our soldering joints were very precise and small, but we hope we can find a better solution to make the overall robot look better and weigh lighter.

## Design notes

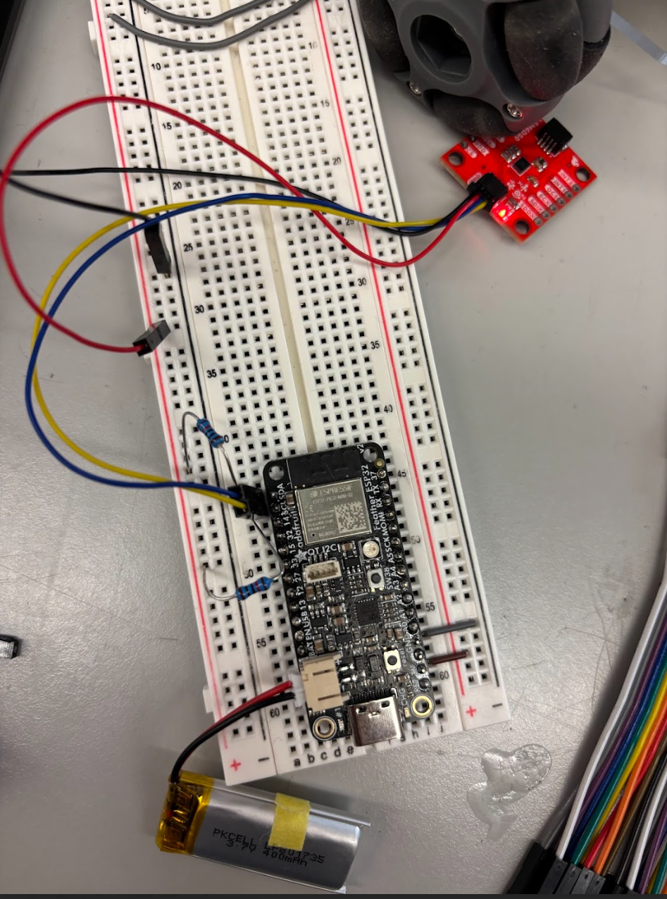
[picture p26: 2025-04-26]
image/prototyping/Screenshot 2025-04-26 140451.png

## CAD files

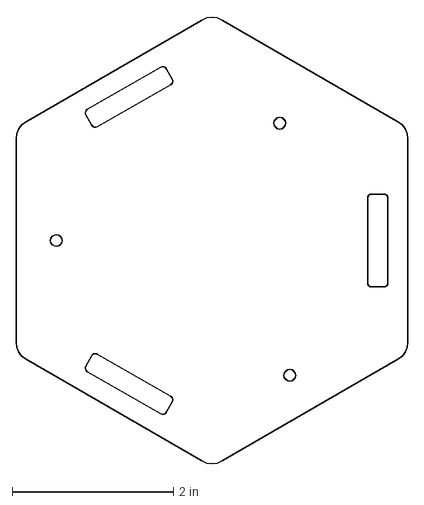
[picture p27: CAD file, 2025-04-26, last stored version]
hardware/top_plate.DXF
4.86 x 5.55 in

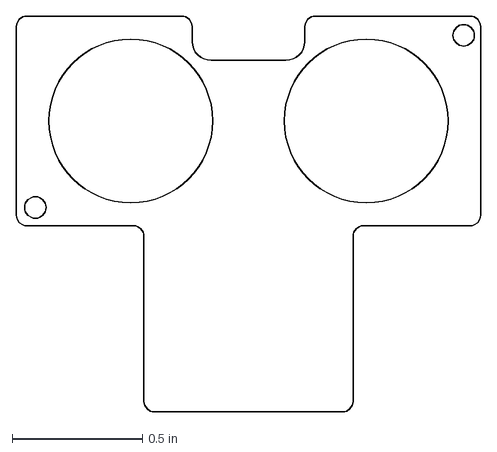
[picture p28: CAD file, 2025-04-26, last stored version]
US sensor.DXF
1.79 x 1.52 in

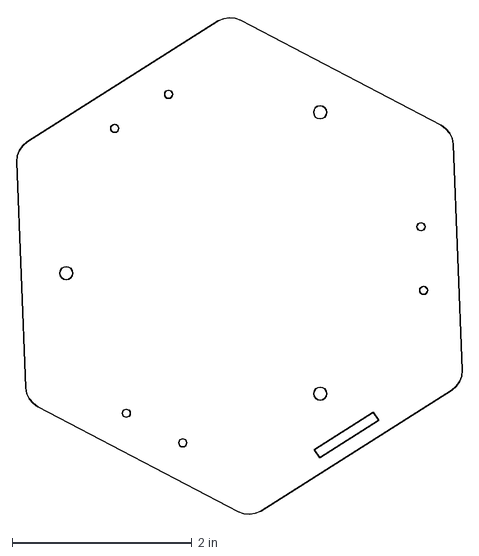
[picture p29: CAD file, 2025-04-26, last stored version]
base_plate.DXF
4.96 x 5.55 in

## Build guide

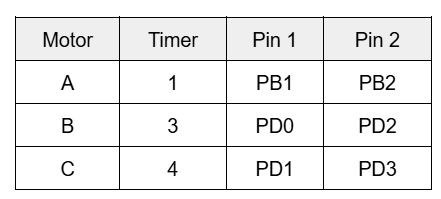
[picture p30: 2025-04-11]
image/wiring_motors.png

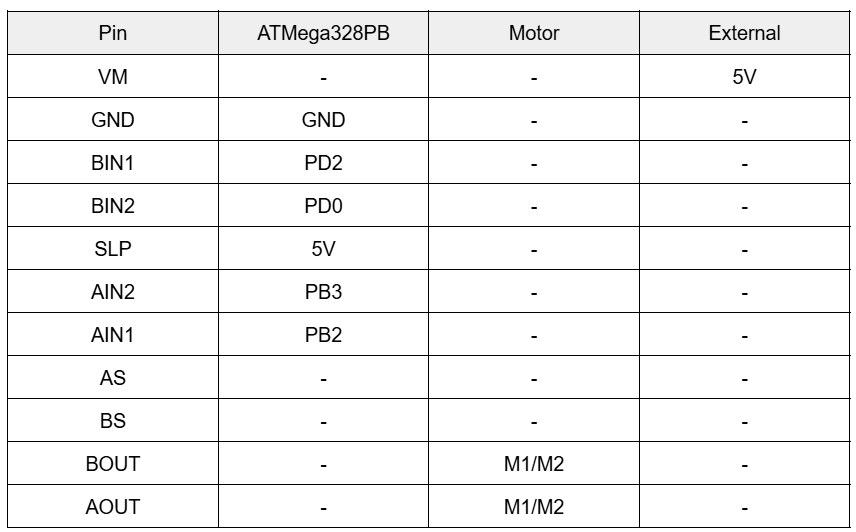
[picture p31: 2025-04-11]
image/wiring_motor_driver.png

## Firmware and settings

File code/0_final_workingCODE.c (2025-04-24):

#define F_CPU 16000000UL
#include <avr/io.h>
#include <util/delay.h>
#include <stdio.h>
#include "uart.h" 
#include <avr/interrupt.h>

#define TRIG_PIN PC2
#define ECHO_PIN PC3
#define BUZZER_PIN PD6

//setting up ultrasonic sensor
volatile uint8_t overflow_counter = 0;
volatile uint8_t timer_ready = 0;

void init() {
    cli();

    DDRC |= (1 << TRIG_PIN);      // TRIG as output
    DDRC &= ~(1 << ECHO_PIN);     // ECHO as input
    DDRD |= (1 << BUZZER_PIN);    // Buzzer pin as output

    // Timer 2: normal mode, prescaler = 64
    TCCR2A = 0x00;
    TCCR2B = (1 << CS22); // Prescaler = 64
    TIMSK2 = 0x00;
    //TIMSK2 = (1 << TOIE2); // Enable overflow interrupt

    sei();
}

void send_pulse() {
    PORTC |= (1 << TRIG_PIN);
    _delay_us(10);
    PORTC &= ~(1 << TRIG_PIN);
}


uint16_t measure_distance() {
    uint16_t ticks;
    overflow_counter = 0;
    TCNT2 = 0;

    while (!(PINC & (1 << ECHO_PIN)));  // Wait for rising edge

    while (PINC & (1 << ECHO_PIN)) {    // Time high pulse
        if (TCNT2 == 255) {
            overflow_counter++;
            TCNT2 = 0;
        }
    }

    ticks = (overflow_counter * 256) + TCNT2;
    uint32_t time_us = ticks * 4; // 4 µs per tick at prescaler 64
    return (uint16_t)(time_us / 58);   // cm
}



void control_buzzer(uint16_t distance_cm) {
    if (distance_cm < 25) {
        PORTD |= (1 << BUZZER_PIN); 
    } else {
         PORTD &= ~(1 << BUZZER_PIN);
    }
}


//states of the direction motor
typedef enum {
    DIR_STOP,
    DIR_FORWARD,
    DIR_BACKWARD,
    DIR_LEFT,
    DIR_RIGHT
} Direction;

Direction current_direction = DIR_STOP;

void SPI_SlaveInit(void) {
    DDRC |= (1<<PC0);   // MISO output
    DDRC &= ~(1<<PC1);  // SCK input
    DDRE &= ~(1<<PE3);  // MOSI input
    DDRE &= ~(1<<PE2);  // SS input
    SPCR1 = (1<<SPE);   // Enable SPI1
}

uint8_t SPI_SlaveReceive(void) {
    while (!(SPSR1 & (1<<SPIF))); // Wait for data
    return SPDR1;
}

//motor setup
 void setup_motorA() {
     DDRB |= (1 << DDB1) | (1 << DDB2);
 
     TCCR1A |= (1 << COM1A1) | (1 << COM1B1);
     TCCR1A |= (1 << WGM11);
     TCCR1B |= (1 << WGM12) | (1 << WGM13);
 
     TCCR1B |= (1 << CS11) | (1 << CS10);
 
     ICR1 = 255;
 
     OCR1A = 0;
     OCR1B = 0;
 }
 
 void setup_motorB() {
     // Set PD0 (OC3A) for PWM, PD4 for direction
     DDRD |= (1 << DDD0) | (1 << DDD4);
 
     // Timer3 setup: Fast PWM Mode 14 using ICR3 as TOP
     TCCR3A = (1 << COM3A1) | (1 << WGM31);                   // Non-inverting PWM on OC3A
     TCCR3B = (1 << WGM32) | (1 << WGM33) | (1 << CS31) | (1 << CS30);                      // Prescaler = 64
 
     ICR3 = 255;      // Set TOP value
     OCR3A = 0;       // Motor off initially
 }
 
 void setup_motorC() {
     // Set PD1 (OC4A) as PWM output, PD3 as DIR output
     DDRD |= (1 << DDD1) | (1 << DDD3);
 
     // Timer4 setup: Fast PWM mode 14, non-inverting on OC4A (PD1)
     TCCR4A = (1 << COM4A1) | (1 << WGM41);                   // Non-inverting PWM on OC4A
     TCCR4B = (1 << WGM42) | (1 << WGM43)                     // Fast PWM mode using ICR4 as TOP
            | (1 << CS41) | (1 << CS40);                      // Prescaler = 64
 
     ICR4 = 255;      // Set PWM TOP value (8-bit style)
     OCR4A = 0;       // Start with motor off
 }
 
 //void motor3_forward() {
 //    PORTD |= (1 << PD1);   // AIN1 = HIGH
 //    PORTD &= ~(1 << PD3);  // AIN2 = LOW
 //}
 //void motor3_reverse() {
 //    PORTD &= ~(1 << PD1);  // AIN1 = LOW
 //    PORTD &= ~(1 << PD3);  // AIN2 = HIGH
 //}
 //void motor3_stop() {
 //    PORTD &= ~(1 << PD1);  // AIN1 = LOW
 //    PORTD &= ~(1 << PD3);  // AIN2 = LOW ? coast
 //}
// void reset_motors() {
//     // Motor A (Timer1)
//     OCR1A = 0;
//     OCR1B = 0;
// 
//     // Motor B (Timer3)
//     OCR3A = 0;
//     OCR3B = 0;
// //    PORTD |= (1 << PD4); 
// 
//     // Motor C (Timer4)
//     OCR4A = 0;
// //    PORTD |= (1 << PD3); 
// }
// 
  void stop_motors_AC() {
     if (current_direction != DIR_STOP) {
        OCR1A = 0;
        OCR1B = 0;
        OCR3A = 0;
        OCR4A = 0;
        PORTD &= ~(1 << PD3); 
        PORTD &= ~(1 << PD4); 
        current_direction = DIR_STOP;
    }
 }
  
 void move_forward(uint8_t duty) {
     if (current_direction != DIR_FORWARD) {
        stop_motors_AC();
        current_direction = DIR_FORWARD;
    }
     
     OCR1A = duty;
     OCR1B = 0;
 
     PORTD |= (1 << PD3); 
     OCR4A = 255 - duty;
 }
 
 void move_backward(uint8_t duty) {
     if (current_direction != DIR_BACKWARD) {
        stop_motors_AC();
        current_direction = DIR_BACKWARD;
    }
 
     // Motor 1 forward
     OCR1A = 0;
     OCR1B = duty;
     
     PORTD &= ~(1 << PD3);  
     OCR4A = duty;  
 }
 void move_right() {
     if (current_direction != DIR_RIGHT) {
        stop_motors_AC();
        current_direction = DIR_RIGHT;
    }
 
     PORTD |= (1 << PD3); 
     OCR4A = 90;
     
     PORTD |= (1 << PD4);   // DIR HIGH ? reverse
     OCR3A = 49;  
     
     OCR1A = 0;
     OCR1B = 0;
     
     // correcting drift
    OCR1A = 0;
    OCR1B = 48;
    _delay_ms(200);
    OCR1A = 48;
    OCR1B = 0;
    _delay_ms(50);
    
//    while (1) {
//         OCR1A = 0;
//         OCR1B = 48;
//         _delay_ms(2000);
//         OCR1A = 48;
//         OCR1B = 0;
//         _delay_ms(500);
//     }
 }
 
 void move_left() {
     if (current_direction != DIR_LEFT) {
        stop_motors_AC();
        current_direction = DIR_LEFT;
    }
 
     OCR1A = 235;
     OCR1B = 0;
 
     PORTD &= ~(1 << PD4);  // DIR LOW
     OCR3A = 255-49;
     
     PORTD &= ~(1 << PD4); 
     
    // correct for drift
    PORTD &= ~(1 << PD3); 
    OCR4A = 55;
    _delay_ms(300);       

    PORTD |= (1 << PD3); 
    OCR4A = 185;
    _delay_ms(100);
//     while (1) {
//         PORTD &= ~(1 << PD3);  // DIR LOW
//         OCR4A = 55;
//         _delay_ms(1500);
//         
//         PORTD |= (1 << PD3); 
//         OCR4A = 185;
//         _delay_ms(500);
//     }
 }
 

 void led(){
     PORTD |= (1 << PD6);
     _delay_ms(500);
     PORTD &= ~(1 << PD6);
 }
 
int main(void) {
//    uart_init();
    
    //ultrasonic sensor
    init();
    
    //motor initialize
    setup_motorA();
    setup_motorB();
    setup_motorC();
     
    SPI_SlaveInit(); 

    uint8_t xl, xh, yl, yh;
    int16_t x, y;
    
//    printf("start\n");
    
    while (1) {       
        SPDR1 = 0x00;
        xl = SPI_SlaveReceive();  // HIGH byte of X
    
        SPDR1 = 0x00;
        xh = SPI_SlaveReceive();  // LOW byte of X
    
        SPDR1 = 0x00;
        yl = SPI_SlaveReceive();  // HIGH byte of Y
    
        SPDR1 = 0x00;
        yh = SPI_SlaveReceive();  // LOW byte of Y
    
        x = (int16_t)((xh << 8) | xl);
        y = (int16_t)((yh << 8) | yl);
        
        //testing motors
//        move_right();
//        _delay_ms(500);
//        
        send_pulse();
        uint16_t dist = measure_distance();
        
//        if (dist < 20) {
//            PORTD |= (1 << BUZZER_PIN);  // Buzzer ON
//
//            if (x > 7500 && y > -4000 && y < 4000) {
//                move_backward(255);
//            } else if (x > -4000 && x < 4000 && y > 7500) {
//                move_right();
//            } else if (x > -4000 && x < 4000 && y < -7500) {
//                move_left();
//            } else {
//                stop_motors_AC();  // Forward or no clear gesture → STOP
//            }
//
//        } else {
//            PORTD &= ~(1 << BUZZER_PIN);  // Buzzer OFF
//
//            if (x < -7500 && y > -4000 && y < 4000) {
//                move_forward(255);
//            } else if (x > 7500 && y > -4000 && y < 4000) {
//                move_backward(255);
//            } else if (x > -4000 && x < 4000 && y > 7500) {
//                move_right();
//            } else if (x > -4000 && x < 4000 && y < -7500) {
//                move_left();
//            } else {
//                stop_motors_AC();
//            }
//        }
        
        
    
        // Debug output for raw bytes and reconstructed values
//        printf("Raw Bytes → XL: %u  XH: %u | YL: %u  YH: %u\r\n", xl, xh, yl, yh);
//        printf("Parsed Accel → X: %d | Y: %d\r\n", x, y);
        
        if (x < -7500 && y > -4000 && y < 4000) {
//             printf("forward\n");
             move_forward(255);
//             led();
         } else if (x > 7500 && y > -4000 && y < 4000) {
//             printf("backward\n");
             move_backward(255);
         } else if (x > -4000 && x < 4000 && y > 7500) {
//             printf("right\n");
             move_right();
         } else if (x > -4000 && x < 4000 && y < -7500) {
//             printf("left\n");
             move_left();
         } else {
//             printf("stop\n");
             stop_motors_AC();
         }
        
        _delay_ms(1000);
    }    

}

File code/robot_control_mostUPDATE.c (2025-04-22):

/*
 * File:   main.c
 * Author: ihuan
 *
 * Created on April 11, 2025, 11:42 AM
 */

 #define F_CPU 16000000UL

 #include <avr/io.h>
 #include <xc.h>
 #include <util/delay.h>
 #include <avr/interrupt.h>
 #include "uart.h"
 
 #define dev_addr 0x6b // device address
 #define OUTX_L_A 0x28  
 #define OUTX_H_A 0x29
 #define OUTY_L_A 0x2A
 #define OUTY_H_A 0x2B
 #define OUTZ_L_A 0x2C
 #define OUTZ_H_A 0x2D
 #define OUTX_L_G 0x22
 #define OUTX_H_G 0x23
 #define OUTY_L_G 0x24
 #define OUTY_H_G 0x25
 #define OUTZ_L_G 0x26
 #define OUTZ_H_G 0x27
 #define CTRL1_XL 0x10
 #define CTRL2_G 0x11
 
 //imu setup
 void I2C_init() {
     TWBR0 = 0x48; // set the bit rate // 100kHz at 16MHz 
     // 100 kHz is the max of lsm i2c standard mode clock frequency
     // datasheet pg13
     // 100 kHz calculated using formula on atmega datasheet 256
     TWCR0 = (1 << TWEN); // enable TWI
     // possibly switch to interrupt based I2C ?
 }
 
 void start_con() {
     // send the start condition
     TWCR0 = (1<<TWINT)| (1<<TWSTA)|(1<<TWEN);
     while(!(TWCR0 & (1<<TWINT))); // wait for the flag to be set
 }
 
 void send(uint8_t data) {
     // send any data onto the I2C bus (could be device address or data)
     TWDR0 = data; 
     TWCR0 = (1<<TWINT) | (1<<TWEN);
     while (!(TWCR0 & (1<<TWINT)));
 }
 
 void stop_con() {
     TWCR0 = (1<<TWINT)| (1<<TWEN)|(1<<TWSTO);
 }
 
 void write_register(uint8_t reg, uint8_t data) {
     start_con(); // start condition
     send(dev_addr<<1); // send device address + W
     send(reg); // send register address
     send(data); // send data to be written
     stop_con();
 }
 
 uint8_t read_register(uint8_t reg) {
     start_con(); // start condition
     send(dev_addr<<1); // send device address + W
     send(reg); // send register address
     start_con(); // repeated start
     send((dev_addr<<1) | 1); // send device address + R
     send(reg); // send register address
     uint8_t data; 
     data = TWDR0; // read data from TWDR0 and return
     return data; 
 }
 
   // set up SPI1 as slave
     // using SPI1 because timers are using PB2
     // need to solder port e
     // set CS as input
 
 void SPI_SlaveInit(void)
 {
    /* Set MISO output, all others input */
    DDRC = (1<<PC0); // MISO / SDO
    DDRC &= ~(1<<PC1); //SCK
    DDRE &= ~(1<<PE3); //MOSI / SDI
    DDRE &= ~(1<<PE2); //CS
    /* Enable SPI */
    SPCR1 = (1<<SPE);
    // don't set mstr bit
 }
 char SPI_SlaveReceive(void)
 {
    /* Wait for reception complete */
    while(!(SPSR1 & (1<<SPIF)));
    /* Return Data Register */
    return SPDR1;
 }
 
 //motor setup
 void setup_motorA() {
     DDRB |= (1 << DDB1) | (1 << DDB2);
 
     TCCR1A |= (1 << COM1A1) | (1 << COM1B1);
     TCCR1A |= (1 << WGM11);
     TCCR1B |= (1 << WGM12) | (1 << WGM13);
 
     TCCR1B |= (1 << CS11) | (1 << CS10);
 
     ICR1 = 255;
 
     OCR1A = 0;
     OCR1B = 0;
 }
 
 void setup_motorB() {
     // Set PD0 (OC3A) for PWM, PD4 for direction
     DDRD |= (1 << DDD0) | (1 << DDD4);
 
     // Timer3 setup: Fast PWM Mode 14 using ICR3 as TOP
     TCCR3A = (1 << COM3A1) | (1 << WGM31);                   // Non-inverting PWM on OC3A
     TCCR3B = (1 << WGM32) | (1 << WGM33) | (1 << CS31) | (1 << CS30);                      // Prescaler = 64
 
     ICR3 = 255;      // Set TOP value
     OCR3A = 0;       // Motor off initially
 }
 
 void setup_motorC() {
     // Set PD1 (OC4A) as PWM output, PD3 as DIR output
     DDRD |= (1 << DDD1) | (1 << DDD3);
 
     // Timer4 setup: Fast PWM mode 14, non-inverting on OC4A (PD1)
     TCCR4A = (1 << COM4A1) | (1 << WGM41);                   // Non-inverting PWM on OC4A
     TCCR4B = (1 << WGM42) | (1 << WGM43)                     // Fast PWM mode using ICR4 as TOP
            | (1 << CS41) | (1 << CS40);                      // Prescaler = 64
 
     ICR4 = 255;      // Set PWM TOP value (8-bit style)
     OCR4A = 0;       // Start with motor off
 }
 
 //void motor3_forward() {
 //    PORTD |= (1 << PD1);   // AIN1 = HIGH
 //    PORTD &= ~(1 << PD3);  // AIN2 = LOW
 //}
 //void motor3_reverse() {
 //    PORTD &= ~(1 << PD1);  // AIN1 = LOW
 //    PORTD &= ~(1 << PD3);  // AIN2 = HIGH
 //}
 //void motor3_stop() {
 //    PORTD &= ~(1 << PD1);  // AIN1 = LOW
 //    PORTD &= ~(1 << PD3);  // AIN2 = LOW ? coast
 //}
 void reset_motors() {
     // Motor A (Timer1)
     OCR1A = 0;
     OCR1B = 0;
 
     // Motor B (Timer3)
     OCR3A = 0;
     OCR3B = 0;
 //    PORTD |= (1 << PD4); 
 
     // Motor C (Timer4)
     OCR4A = 0;
 //    PORTD |= (1 << PD3); 
 }
 
 void move_backward(uint8_t duty) {
     reset_motors();
     
     OCR1A = duty;
     OCR1B = 0;
 
     PORTD |= (1 << PD3); 
     OCR4A = 255 - duty;
 }
 
 void move_forward(uint8_t duty) {
     reset_motors();
 
     // Motor 1 forward
     OCR1A = 0;
     OCR1B = duty;
     
     PORTD &= ~(1 << PD3);  
     OCR4A = duty;  
 }
 void move_right() {
     reset_motors();
 
     PORTD |= (1 << PD3); 
     OCR4A = 90;
     
     PORTD |= (1 << PD4);   // DIR HIGH ? reverse
     OCR3A = 49;  
     
     while (1) {
         OCR1A = 0;
         OCR1B = 48;
         _delay_ms(2000);
         OCR1A = 48;
         OCR1B = 0;
         _delay_ms(500);
     }
 }
 
 void move_right_notGood() {
     reset_motors();
 
     PORTD |= (1 << PD3); 
     OCR4A = 55;
     
     PORTD |= (1 << PD4);   // DIR HIGH ? reverse
     OCR3A = 255-49;  
     
     while (1) {
         OCR1A = 0;
         OCR1B = 48;
         _delay_ms(1250);
         OCR1B = 0;
         _delay_ms(1500);
     }
 }
 void move_left() {
     reset_motors();
 
     OCR1A = 235;
     OCR1B = 0;
 
     PORTD &= ~(1 << PD4);  // DIR LOW
     OCR3A = 255-49;
 
     while (1) {
         PORTD &= ~(1 << PD3);  // DIR LOW
         OCR4A = 55;
         _delay_ms(1500);
         
         PORTD |= (1 << PD3); 
         OCR4A = 185;
         _delay_ms(500);
     }
 }
 
 void move_left_notGood() {
     reset_motors();
     
     OCR1A = 204;
     OCR1B = 0;
 
     PORTD &= ~(1 << PD3);  
     OCR4A = 50; 
     
     //motor 3
     PORTD &= ~(1 << PD4);  // DIR LOW ? forward
     OCR3A = 255 - 195; 
 }
 
 void stop_motors_AC() {
     OCR1A = 0;
     OCR1B = 0;
     OCR3A = 0;
     OCR3B = 0;
     OCR4A = 0;
     PORTD |= (1 << PD3); 
     PORTD |= (1 << PD4); 
 }
 
 int main(void) {
     //motor initialize
     setup_motorA();
     setup_motorB();
     setup_motorC();
     
     //imu intiialize
     I2C_init(); 
 //    uart_init(); 
     write_register(CTRL1_XL, (1<<6)); // 104 Hz set up accel
     write_register(CTRL2_G, (1<<6)); // 104 Hz set up gyro
     
     SPI_SlaveInit(); 
     
 //    uint8_t rxData; 
     
     uint8_t x_l, x_h, y_l, y_h;
     int16_t x, y;
    
     while (1) {
         SPDR1 = 0x22; // data to send to esp32
 //        rxData = SPI_SlaveReceive();
         
         //data from esp for IMU
         x_l = SPI_SlaveReceive();
         x_h = SPI_SlaveReceive();
         x = (int16_t) (x_h<<8) | (x_l); // combine high and low registers
         //printf("%d\n", x);
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

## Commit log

2025-03-24 Add BOM
2025-04-11 i2c working code
2025-04-11 imu update on sprint review
2025-04-11 add gyroscope imu
2025-04-11 activate gyro
2025-04-11 added flex sensor test code
    [test_flexsensor.c]
2025-04-11 added motor codes
2025-04-11 updated sprint with motor
2025-04-11 motor wiring
2025-04-11 add imu testing image
2025-04-16 add esp32 tx rx code
2025-04-18 spi code (esp32 side not working, not transmitting)
2025-04-18 added calibrated imu
2025-04-18 updated imu graphs
2025-04-18 detail hardware implemnetaton and added IMU motor control code
2025-04-21 change atmega spi to slave
2025-04-22 added the SPI part into robot control, also fine tuned the basic 4 directions
2025-04-22 updated wireless control - works from IMU to both feather, issue from robot feather to atemega
    [A_feather_to_IMU_wireless.ino, A_feather_to_robot_sendsAtmega.ino]
2025-04-22 working wireless
2025-04-23 updated classficiation with wireless IMU
2025-04-24 added sensor timer0
2025-04-24 working led distance sensor code added
2025-04-24 aded sensor integration
2025-04-24 changed led code
2025-04-24 updates integrate led
2025-04-24 wokring code, that switches direction well
2025-04-26 added validatioin
    [Backward.xlsx, Forward.xlsx, IMU Still.xlsx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]
2025-04-26 add laser cut files
    [US sensor.DXF, base_plate.DXF, top_plate.DXF]
2025-04-26 added laser cut files
    [US sensor.DXF, base_plate.DXF, top_plate.DXF]
2025-04-26 deleted stuff to fit file size limit
    [Backward.xlsx, Forward.xlsx, IMU Still.xlsx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]
